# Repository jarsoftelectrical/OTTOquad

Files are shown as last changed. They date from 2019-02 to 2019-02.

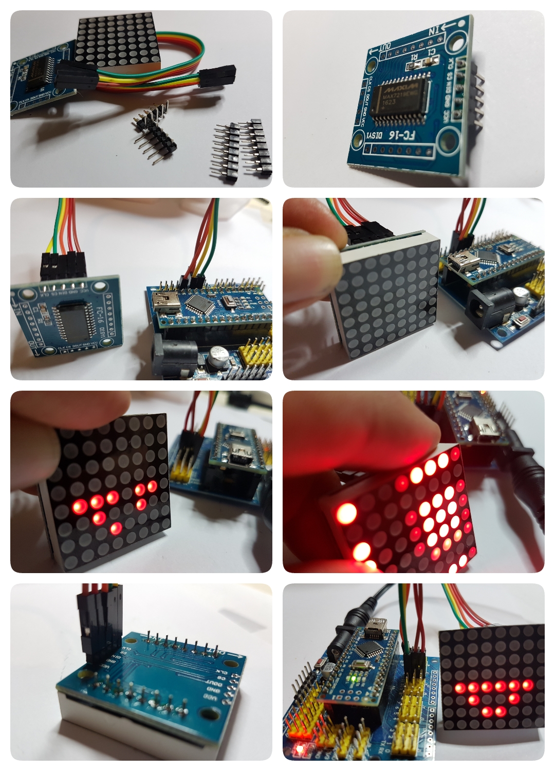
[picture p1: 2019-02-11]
Assembly/2017122816261731570.jpg

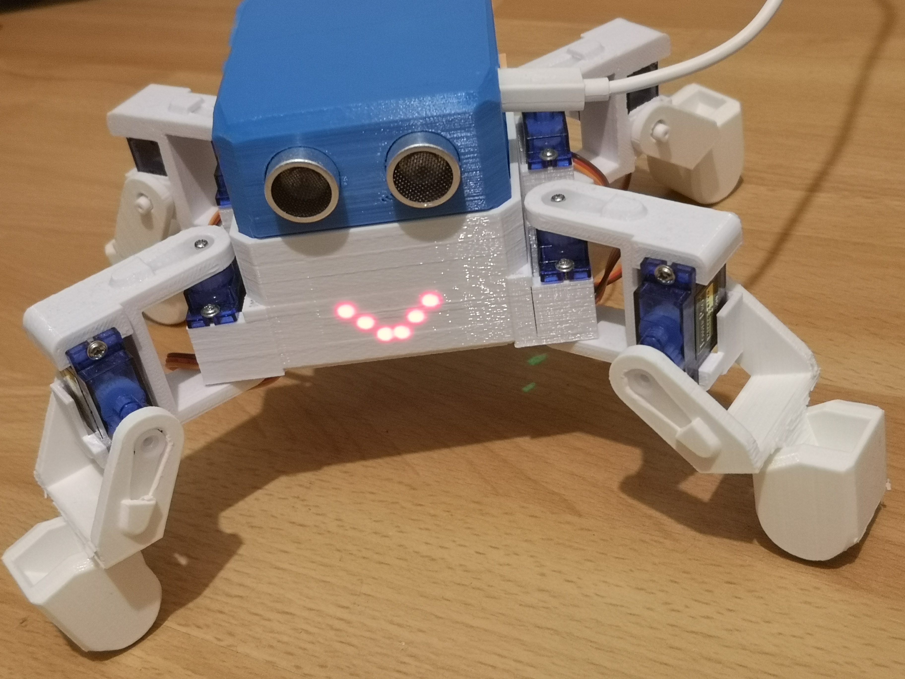
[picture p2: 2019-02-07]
Pictures/IMG_20190207_202704 1.jpg

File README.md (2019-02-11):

# OTTO Quad Code and STL files   firmware 9

Arduino Libraries and Sketch, Some basic instructions also included

## Info

Otto Quad

Compatible with parts of the OTTO android APP and the OTTO desktop control which can be downloaded from another of my repros (windows OS only)

As an open source library, Otto and Myself respect all contributors to the open source community and thank you very much for everyone's supervision.

If you have a question then please post it to the Otto Builder facebook group, this is also a great place for help and advice.

### How to print:
You will to print:
- 1 x Head (two versions available, Nano I/O shield and GSTDuino)
- 1 x Body 7 A (body)
- 2 x M-Hips (Legs)
- 2 x M-Hips SHAFTS (Pins - 4 needed in total)
- 1 x M-Body SHAFTS (Pins - 4 needed in total)
- 2 x Single_foot_typeA
- 2 x Single_foot_typeB (feet)

Print your Otto Quad, 
- 20% infil
- supports for the feet Only as they need to printed as they are provided
- I use a RAFT to help stick to the bed, this is optional
- There should be no need to rotate any parts, print as they are shown.

### Parts Needed:

Parts required for Otto Quad, 
- 8 x SG90 SERVOS
- Arduino NANO   atmega328 version
- Arduino NANO I/O shield
- HC SR04 ultrasonic module
- MAX7219 dot matrix module
- Female to female hook-up wires
- Bluetooth module (optional)
- LIPO battery 3.7volt and a suitable DC-DC converter module (optional)
- GSTDUINO PCB (instead of the Arduino Nano and shield, OPTIONAL)

### Revision of history:

Software Version 9 of the libraries, initial release

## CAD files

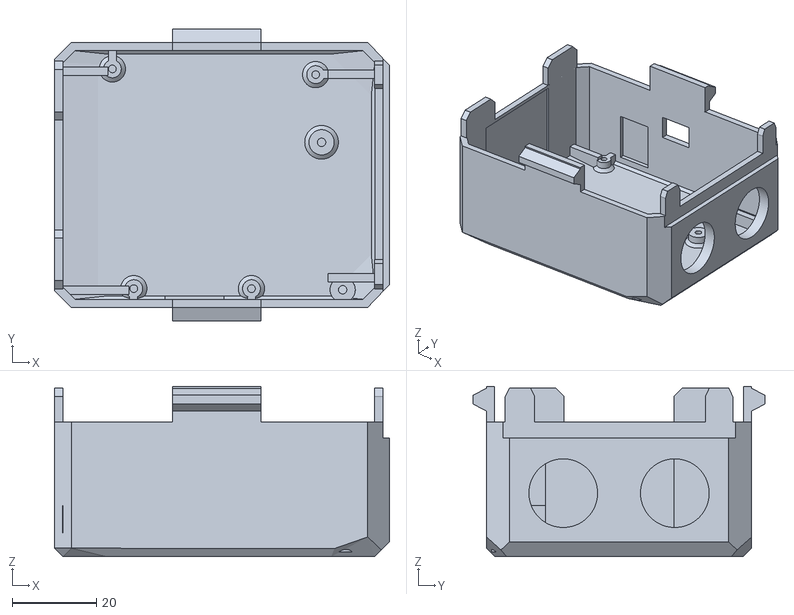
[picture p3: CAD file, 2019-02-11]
STL/Head_NANO_SHIELD.stl
79.5 x 69.2 x 40.4

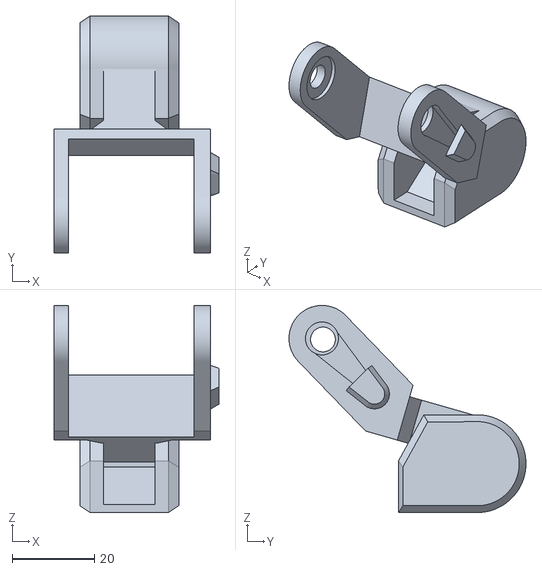
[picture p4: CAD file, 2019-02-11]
STL/Single_foot _typeA.stl
40.0 x 57.5 x 50.2

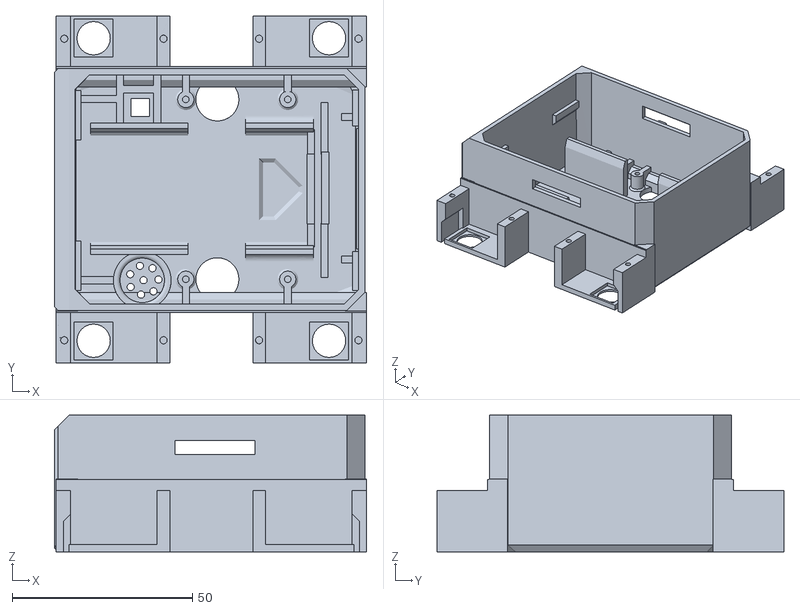
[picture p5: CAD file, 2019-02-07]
STL/Body_7A.stl
86.5 x 96.1 x 37.9

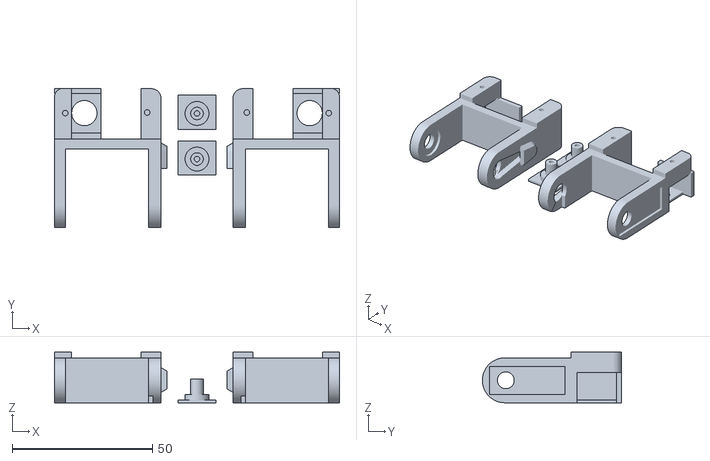
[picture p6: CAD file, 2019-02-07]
STL/m-hips.stl
101.5 x 49.6 x 18.0

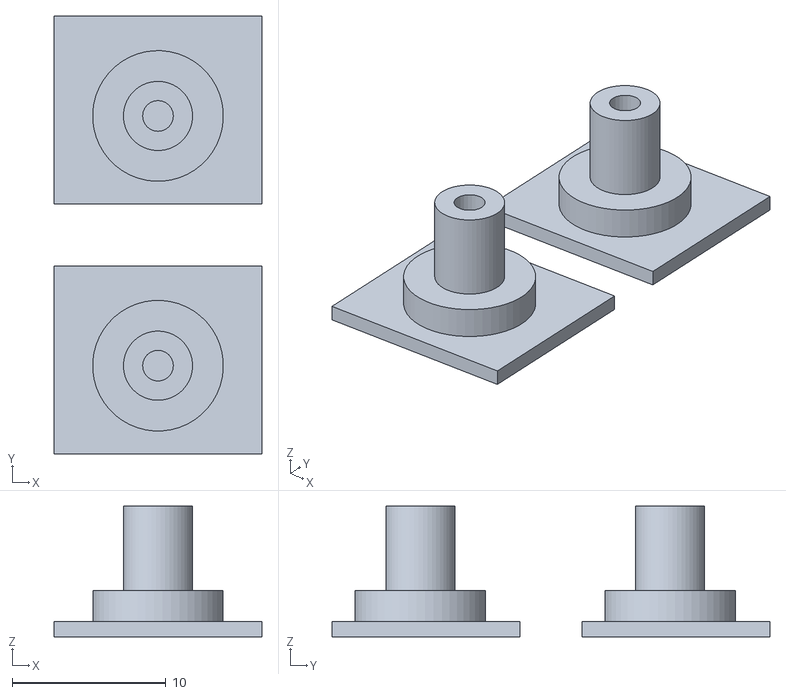
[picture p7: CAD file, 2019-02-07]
STL/m-hips_SHAFTS.stl
13.5 x 28.5 x 8.50

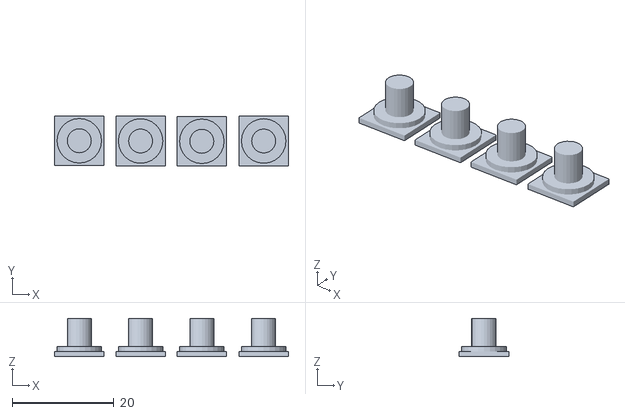
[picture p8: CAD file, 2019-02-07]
STL/m-body-shafts.stl
46.0 x 9.86 x 7.50

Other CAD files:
STL/Single_foot _typeB.stl
STL/Head.stl

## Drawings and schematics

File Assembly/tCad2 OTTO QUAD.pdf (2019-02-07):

## ULTRASONIC MODULE

## SERVO'S

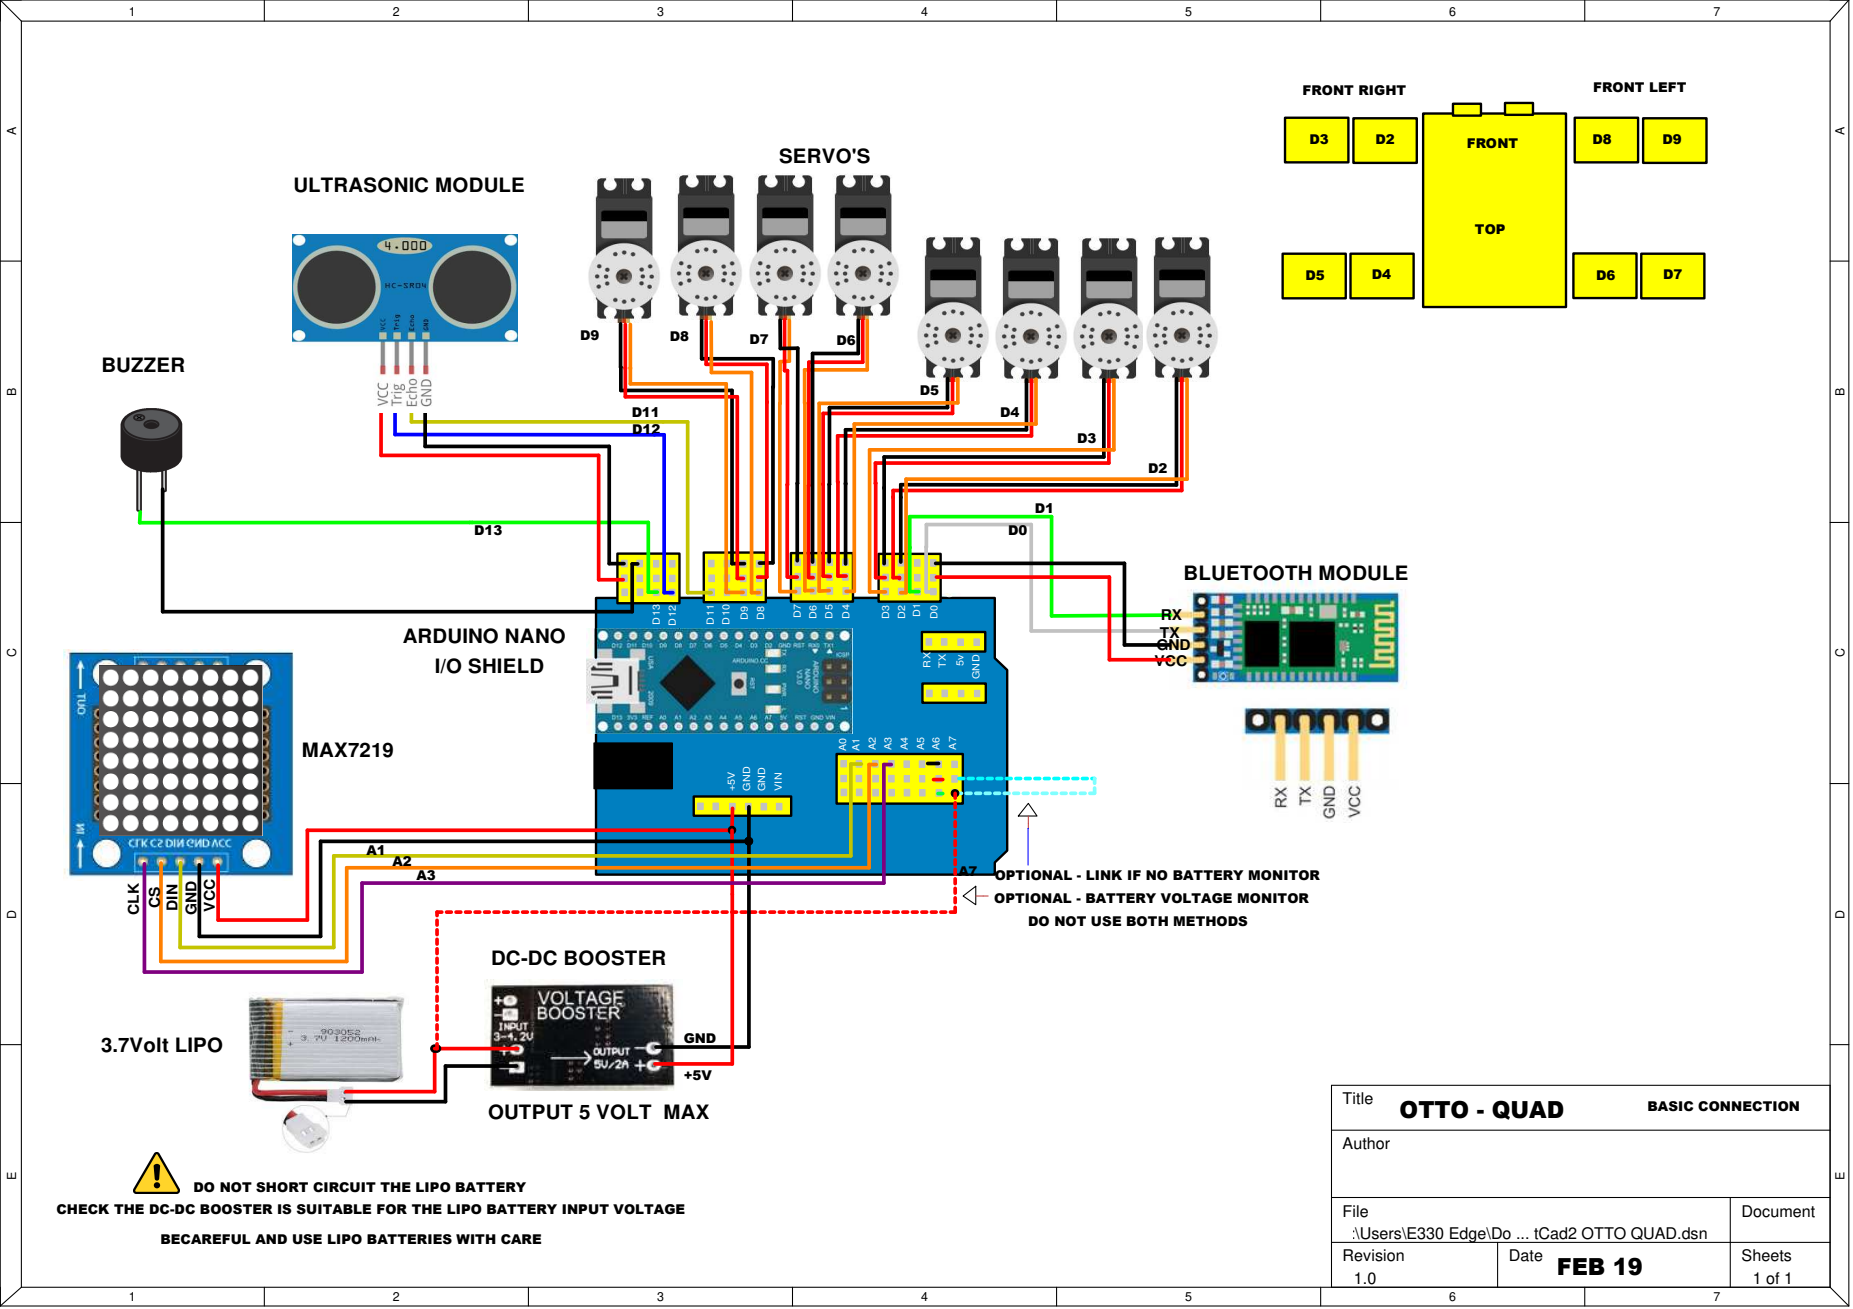
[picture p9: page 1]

A1
A2
A3

OPTIONAL - LINK IF NO BATTERY MONITOR

OPTIONAL - BATTERY VOLTAGE MONITOR

DO NOT USE BOTH METHODS

DO NOT SHORT CIRCUIT THE LIPO BATTERY

CHECK THE DC-DC BOOSTER IS SUITABLE FOR THE LIPO BATTERY INPUT VOLTAGE

File C:\Users\E330 Edge\Do ... tCad2 OTTO QUAD.dsn | Document

BECAREFUL AND USE LIPO BATTERIES WITH CARE

Revision 1.0 | Date FEB 19 | Sheets 1 of 1

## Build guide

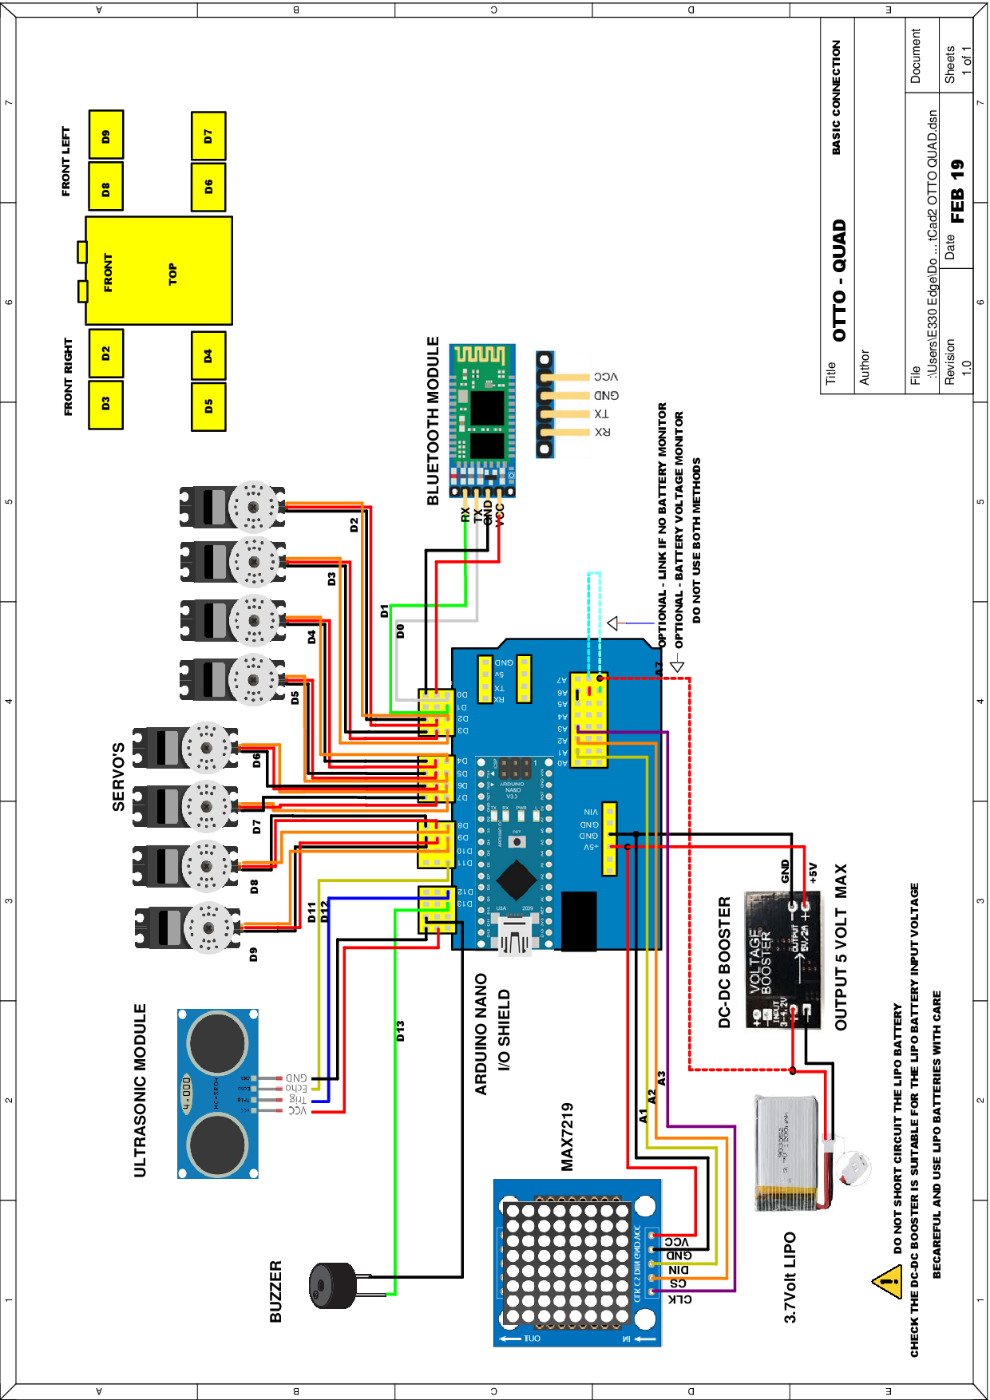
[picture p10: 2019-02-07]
Assembly/tCad2 OTTO QUAD.png

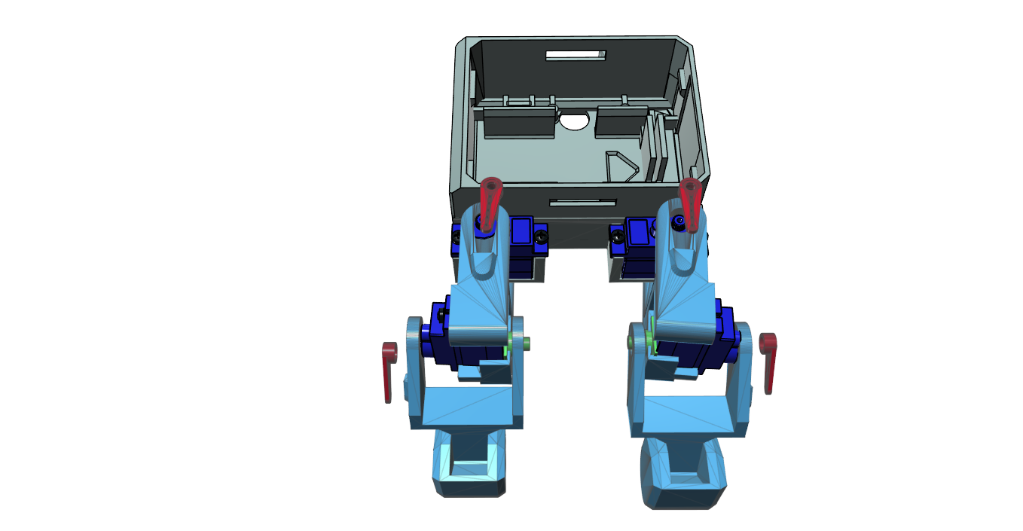
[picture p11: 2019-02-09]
Assembly/Assembly_6.png

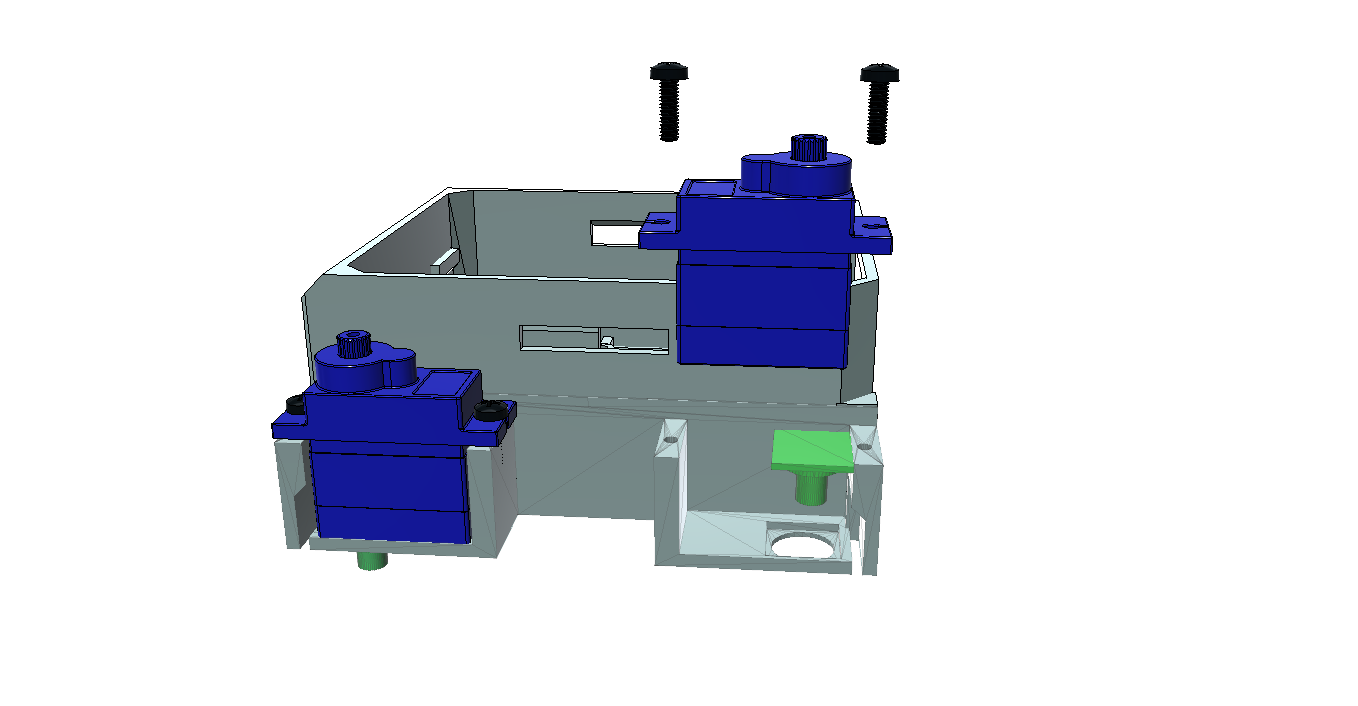
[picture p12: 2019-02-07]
Assembly/Assembly_2.png

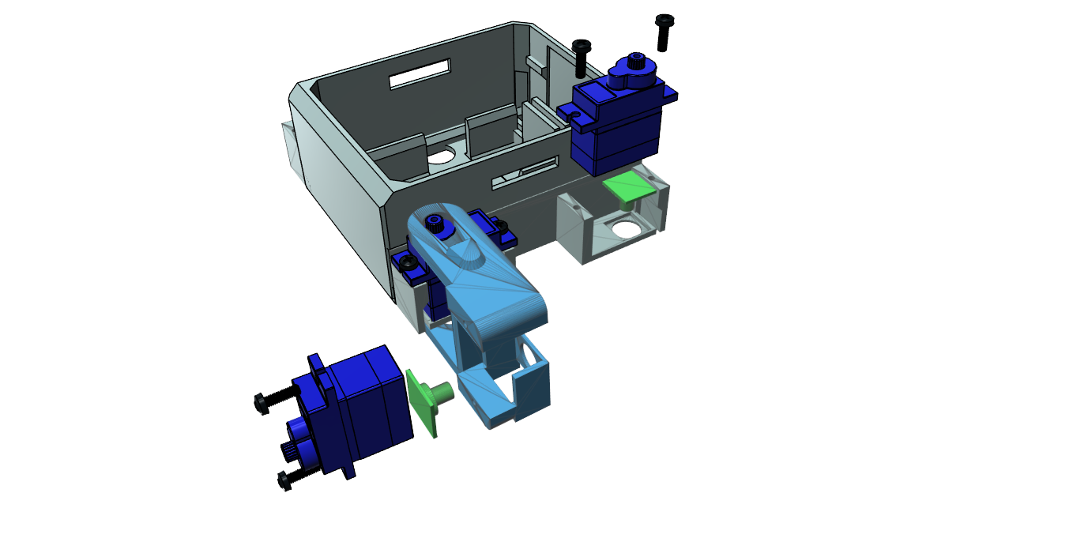
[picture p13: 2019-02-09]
Assembly/Assembly_3.png

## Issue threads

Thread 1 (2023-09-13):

Error in the model: Body_7A.stl

tekasijimo, 2023-09-13:
Hello friend! There is an error in the Body_7A.stl model! One of the sides for mounting the servo is not fully connected to the main part of the case. Because of this, when printing, it is printed as a separate element and is not connected to the case. I could fix this if there were sources, since editing the STL is inconvenient and my software does not allow doing it in an adequate way. If it is possible, in addition to the STL, add another folder with OBJ files, then it will be easier to eliminate errors and also allow you to upgrade the case for other elements.
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

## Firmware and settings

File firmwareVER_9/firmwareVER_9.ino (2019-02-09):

#include <setjmp.h>
//#include "US.h"
#include "OTTOKame.h"
#include "MaxMatrix.h"
MaxMatrix ledmatrix=MaxMatrix(A1,A2,A3, 1); //PIN  A1=DIN, PIN A2=CS, PIN A3=CLK
//-- Library to manage serial commands
#include <OttoSerialCommand.h>
OttoSerialCommand SerialCmd;  //The SerialCommand object


#define CAL_TRIGGER_PIN 10 // link this PIN 10 to +5V to enter set up mode
#define LED_PIN 13
#define PIN_Buzzer  13
//#define PIN_NoiseSensor A6
//#define battery A7
#define TIME_INTERVAL 5000
/*
   (servo PIN CONNECTIONS)
   __________ __________ _________________
  |(pin9)_____)(pin8)  (pin2)(______(pin3)|
  |__|       |left FRONT right|        |__|
             |                |
             |                |
             |                |
   _________ |                | __________
  |(pin7)_____)(pin6)__(pin4)(______(pin5)|
  |__|                                 |__|
  
ULTRASONIC PIN_Trigger 12
ULTRASONIC PIN_Echo    11
BUZZER PIN 13
*/
MiniKame robot;
bool obstacleDetected = false;
int T=1000;              //Initial duration of movement
int moveId=0;            //Number of movement
int modeId=0;            //Number of mode
int moveSize=15;         //Asociated with the height of some movements
bool auto_mode = false;
bool random_walk = false;
bool stopSerial = false;
unsigned long cur_time, prev_serial_data_time, perv_sensor_time;
char cmd = 's';
static char prev_cmd = '.';
const char programID[]="Otto_KAME7"; //Each program will have a ID
jmp_buf jump_env;
int randomDance=0;
//---------------------------------------------------------
//-- Otto has 5 modes:
//--    * MODE = 0: Otto is awaiting  
//--    * MODE = 1: Dancing mode!  
//--    * MODE = 2: Obstacle detector mode  
//--    * MODE = 3: Noise detector mode   
//--    * MODE = 4: OttoPAD or any Teleoperation mode (listening SerialPort). 
//---------------------------------------------------------
volatile int MODE=4; //State of Otto in the principal state machine. 

void setup() {
  
  //Serial communication initialization
  Serial.begin(9600);  
  // set up Matrix display
  ledmatrix.init();
  ledmatrix.setIntensity(1);

  randomSeed(analogRead(A6));
  //
  robot.init(PIN_Buzzer);
  delay(2000);
  //MY servo 2 needed to be reversed so we do it here after the init 
  //robot.reverseServo(0);
  //robot.reverseServo(1);
  robot.reverseServo(2);
  //robot.reverseServo(3);
  //robot.reverseServo(4);
  //robot.reverseServo(5);
  //robot.reverseServo(6);
  //robot.reverseServo(7);
  { //begin:  servo calibrating if PIN 10 is HIGH
    bool state = true;
    pinMode(CAL_TRIGGER_PIN, OUTPUT);
    digitalWrite(CAL_TRIGGER_PIN, 0);
    pinMode(CAL_TRIGGER_PIN, INPUT);
    while (digitalRead(CAL_TRIGGER_PIN)) {
       robot.home();//Otto HOME position
      digitalWrite(LED_PIN, 1); // on calibrating SOUND BUZZER, sounds every 2 seconds
      delay(100);
      digitalWrite(LED_PIN, 0); // off calibrating STOP BUZZER
      delay(2000);
      robot.refresh();
      state = !state;
    }
    digitalWrite(LED_PIN, 0); // off calibrating STOP BUZZER
  }//end:
  perv_sensor_time = prev_serial_data_time = millis();
  //robot.run();
  //robot.turnL();
  //robot.turnR();
  //robot.pushUp();
  //robot.upDown();
  //robot.dance();
  //robot.frontBack();
  //robot.moonwalkL();
  //robot.omniWalk();
  //robot.hello();
  //robot.jump();
  // Animation Uuuuuh - A little moment of initial surprise
 //-----
  for(int i=0; i<2; i++){
      for (int i=0;i<8;i++){  
        robot.putAnimationMouth(littleUuh,i);
        delay(150);
      }
  }
    //Smile for a happy Otto :)
    robot.putMouth(smile);
    robot.sing(S_happy);
    delay(200);  

    //Setup callbacks for SerialCommand commands 
  SerialCmd.addCommand("S", receiveStop);      //  sendAck & sendFinalAck
  SerialCmd.addCommand("L", receiveLED);       //  sendAck & sendFinalAck
  SerialCmd.addCommand("M", receiveMovement);  //  sendAck & sendFinalAck
  SerialCmd.addCommand("H", receiveGesture);   //  sendAck & sendFinalAck
  SerialCmd.addCommand("K", receiveSing);      //  sendAck & sendFinalAck
  SerialCmd.addCommand("D", requestDistance);
  //SCmd.addCommand("B", requestBattery);   // 
  SerialCmd.addCommand("I", requestProgramId);
  SerialCmd.addCommand("J", requestMode);
  SerialCmd.addDefaultHandler(receiveStop);
}
///////////////////////////////////////////////////////////////////
//-- Principal Loop ---------------------------------------------//
///////////////////////////////////////////////////////////////////
void loop() {

 if (Serial.available()>0 && MODE!=4){
    SerialCmd.readSerial();  
    //MODE=4;
    robot.putMouth(happyOpen);
  }
  
    switch (MODE) {

      //-- MODE 0 - Otto is awaiting
      //---------------------------------------------------------
      case 0:
      

        break;
      

      //-- MODE 1 - Dance Mode!
      //---------------------------------------------------------
      case 1:
        randomDance=random(5,15); //5,20
       if (randomDance == 5) randomDance = 6;
        robot.putMouth(random(10,21));
        robot.home();//Otto stop
        pause(750);
        gaits(randomDance);
        
        pause(8000);
        break;


      //-- MODE 2 - Obstacle detector mode
      //---------------------------------------------------------
      case 2:
       robot.run(0); //Otto walk straight
            //robot.refresh();
            robot.putMouth(smile);
            pause(500);
            obstacleDetector();
            pause(500);
            
        if(obstacleDetected){

             robot.home();//Otto stop
             robot.putMouth(bigSurprise);
             pause(3000);
             robot.putMouth(xMouth);
             robot.run(1); //Otto walk back
             pause(3000);
             robot.putMouth(sad);
             robot.home();//Otto stop
             pause(3000);
             robot.turnL(1, 550);
             pause(3000);
             obstacleDetector();
        }

          robot.refresh();
        break;


      //-- MODE 3 - Noise detector mode
      //---------------------------------------------------------  
      case 3:
       
        
        break;
        

      //-- MODE 4 - OttoPAD or any Teleoperation mode (listening SerialPort) 
      //---------------------------------------------------------
      case 4:

        SerialCmd.readSerial();
        
        //If Otto is moving yet
        if (robot.getRestState()==false){  
          //move(moveId);
         
          gaits(moveId);
        }

         
          
       robot.refresh();
      
        break;      


      default:
          MODE=0;
          break;
    }

}
//////////////////////////////////////////////////////////////////////////
void  gaits(int cmd) 
{
  
  bool manualMode = false;
    
    bool taken = true;
    if (prev_cmd == cmd) return;

    switch (cmd) 
    {
      case 1:
      //MiniKame::run(int dir, float steps, float T) 
        robot.run(0);
        break;
      case 2:
        robot.run(1);
        break;
      case 3:
        robot.turnL(1, 550);
        break;
      case 4:
        robot.turnR(1, 550);
        break;
      case 5:
        robot.home();
        break;
      case 6:
        robot.pushUp();
        break;
      case 7:
        robot.upDown();
        break;
      case 8:
        robot.waveHAND();
        break;
      case 9:
        robot.Hide();
        break;
      case 10:
        robot.omniWalk(true);
        break;
      case 11:
        robot.omniWalk(false);
        break;
      case 12:
        robot.dance(1, 1000);
        break;
      case 13:
       robot.frontBack(1, 750);
        break;
      case 14:
       robot.jump();
        break;
        case 15:
       robot.scared();
        break;

      default:
        taken = false;
        manualMode = true;
    }
     if(!manualMode){
    sendFinalAck();

  }
  if (taken) prev_cmd = cmd;
  return taken;
}
////////////////////////////////////////////////////////////////////
void pause(int period) 
  {
    long timeout = millis() + period;
    do 
      {
      robot.refresh();
    } 
    while (millis() <= timeout);
  }
///////////////////////////////////////////////////////////////////
//-- Functions --------------------------------------------------//
///////////////////////////////////////////////////////////////////

//-- Function to read distance sensor & to actualize obstacleDetected variable
void obstacleDetector(){

   int distance = robot.getDistance();

        if(distance<15){
          obstacleDetected = true;
        }else{
          obstacleDetected = false;
        }
}
//-- Function to receive Stop command.
void receiveStop(){

    sendAck();
    robot.home();
    prev_cmd  = '.';
    sendFinalAck();

}
//-- Function to send Ack comand (A)
void sendAck(){

  delay(30);

  Serial.print(F("&&"));
  Serial.print(F("A"));
  Serial.println(F("%%"));
  Serial.flush();
}


//-- Function to send final Ack comand (F)
void sendFinalAck(){

  delay(30);

  Serial.print(F("&&"));
  Serial.print(F("F"));
  Serial.println(F("%%"));
  Serial.flush();
}
//-- Function to receive movement commands
void receiveMovement(){
    sendAck();
    
    if (robot.getRestState()==true){
        robot.setRestState(false);
    }

    robot.clearMouth();
    //Definition of Movement Bluetooth commands
    //M  MoveID  T   MoveSize  
    char *arg; 
    arg = SerialCmd.next(); 
    if (arg != NULL) {
      moveId=atoi(arg);
      robot.putMouth(smile);
      }
    else{
      robot.putMouth(xMouth); // bad command
      delay(2000);
      robot.clearMouth();
      moveId=0; //stop
    }
    
    arg = SerialCmd.next(); 
    if (arg != NULL) {T=atoi(arg);}
    else{
      T=1000;
    }

    arg = SerialCmd.next(); 
    if (arg != NULL) {moveSize=atoi(arg);}
    else{
      moveSize =15;
    }
}
//-- Function to receive LED commands
void receiveLED(){  

    //sendAck & stop if necessary
    sendAck();
    robot.home();

    //Examples of receiveLED Bluetooth commands
    //L 000000001000010100100011000000000
    //L 001111111111111111111111111111111 (todos los LED encendidos)
    unsigned long int matrix;
    char *arg;
    char *endstr;
    arg=SerialCmd.next();
    //Serial.println (arg);
    if (arg != NULL) {
      matrix=strtoul(arg,&endstr,2);    // Converts a char string to unsigned long integer
      robot.putMouth(matrix,false);
    }else{
      robot.putMouth(xMouth); // bad command
      delay(2000);
      robot.clearMouth();
    }

    sendFinalAck();

}
//-- Function to receive sing commands
void receiveSing() {
  //sendAck & stop if necessary
  sendAck();
   robot.home();

  //Definition of Sing Bluetooth commands
  //K  SingID
  int sing = 0;
  char *arg;
  arg = SerialCmd.next();
  if (arg != NULL) sing = atoi(arg);
  else  {
  robot.putMouth(xMouth); // bad command   
  delay(2000); // 
  robot.clearMouth();
  }
  

  switch (sing) {
    case 1: //K 1
      robot.sing(S_connection);
      break;
    case 2: //K 2
      robot.sing(S_disconnection);
      break;
    case 3: //K 3
      robot.sing(S_surprise);
      break;
    case 4: //K 4
      robot.sing(S_OhOoh);
      break;
    case 5: //K 5
      robot.sing(S_OhOoh2);
      break;
    case 6: //K 6
      robot.sing(S_cuddly);
      break;
    case 7: //K 7
      robot.sing(S_sleeping);
      break;
    case 8: //K 8
      robot.sing(S_happy);
      break;
    case 9: //K 9
      robot.sing(S_superHappy);
      break;
    case 10: //K 10
      robot.sing(S_happy_short);
      break;
    case 11: //K 11
      robot.sing(S_sad);
      break;
    case 12: //K 12
      robot.sing(S_confused);
      break;
    case 13: //K 13
      robot.sing(S_fart1);
      break;
    case 14: //K 14
      robot.sing(S_fart2);
      break;
    case 15: //K 15
      robot.sing(S_fart3);
      break;
    case 16: //K 16
      robot.sing(S_mode1);
      break;
    case 17: //K 17
      robot.sing(S_mode2);
      break;
    case 18: //K 18
      robot.sing(S_mode3);
      break;
    case 19: //K 19
      robot.sing(S_buttonPushed);
      break;
    default:
      break;
  }
  sendFinalAck();
}

//-- Function to send ultrasonic sensor measure (distance in "cm")
void requestDistance(){

    robot.home();  //stop if necessary  

    int distance = robot.getDistance();
    Serial.print(F("&&"));
    Serial.print(F("D "));
    Serial.print(distance);
    Serial.println(F("%%"));
    Serial.flush();
}
//-- Function to send battery voltage percent
void requestBattery(){

    robot.home();  //stop if necessary

    //The first read of the batery is often a wrong reading, so we will discard this value. 
    double batteryLevel = robot.getBatteryLevel();

    Serial.print(F("&&"));
    Serial.print(F("B "));
    Serial.print(batteryLevel);
    Serial.println(F("%%"));
    Serial.flush();
}


//-- Function to send program ID
void requestProgramId(){

    robot.home();   //stop if necessary

    Serial.print(F("&&"));
    Serial.print(F("I "));
    Serial.print(programID);
    Serial.println(F("%%"));
    Serial.flush();
}
//-- Function to receive mode selection.
void requestMode(){

    sendAck();
    robot.home();
    //Definition of Mode Bluetooth commands
    //J ModeID    
    char *arg; 
    arg = SerialCmd.next(); 
    if (arg != NULL) 
    {
      modeId=atoi(arg);
      robot.putMouth(heart);
      delay(1000);
      robot.clearMouth();
      }
    else{
      robot.putMouth(xMouth); // bad command
      delay(2000);
      robot.clearMouth();
      modeId=0; //stop
    }
switch (modeId) {
      case 0: //
        MODE = 0;
        break;
      case 1: //
        MODE = 1;
        robot.sing(S_mode1);
        robot.putMouth(one);
        delay(1000);
    delay(200);
        break;
        case 2: //
        MODE = 2;
        robot.sing(S_mode2);
        robot.putMouth(two);
        delay(1000);
        break;
        case 3: //
        MODE = 3;
        robot.sing(S_mode3);
        robot.putMouth(three);
        delay(1000);        
        break;
        case 4: //
        robot.sing(S_mode1);
        robot.putMouth(four);
        delay(1000);       
        MODE = 4;
        break;
     default:
        MODE = 0;
        break;
   }
sendFinalAck();
robot.clearMouth();
robot.putMouth(smile);

}
 
//-- Function to receive gesture commands
void receiveGesture(){

    //sendAck & stop if necessary
    sendAck();
    robot.home(); 

    //Definition of Gesture Bluetooth commands
    //H  GestureID  
    int gesture = 0;
    char *arg; 
    arg = SerialCmd.next(); 
    if (arg != NULL) {gesture=atoi(arg);}
    else 
    {
      robot.putMouth(xMouth);
      delay(2000);
      robot.clearMouth();
    }

    switch (gesture) {
      case 1: //H 1 
        robot.playGesture(OttoHappy);
        break;
      case 2: //H 2 
        robot.playGesture(OttoSuperHappy);
        break;
      case 3: //H 3 
        robot.playGesture(OttoSad);
        break;
      
      case 7: //H 7 
        robot.playGesture(OttoLove);
        break;   
      
        
      default:
        break;
    }

    sendFinalAck();
}

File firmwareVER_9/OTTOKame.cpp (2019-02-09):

#include <EEPROM.h>
#include "OTTOKame.h"

/*
   (servo index, pin to attach pwm)
   __________ __________ _________________
  |(3,9)_____)(1,8)      (0,2)(______(2,3)|
  |__|       |left FRONT right|        |__|
             |                |
             |                |
             |                |
   _________ |                | __________
  |(7,7)_____)(5,6)______(4,4)(______(6,5)|
  |__|                                 |__|

*/
//comment below manually setting trim in MiniKame() constructor
#define __LOAD_TRIM_FROM_EEPROM__
#define EEPROM_MAGIC  0xabcd
#define EEPROM_OFFSET 2   //eeprom starting offset to store trim[]

// FRONT_RIGHT_HIP servo 0  Pin 2
// FRONT_LEFT_HIP servo 1  Pin 8
// FRONT_RIGHT_LEG servo 2  Pin 3
// FRONT_LEFT_LEG servo 3  Pin 9
// BACK_RIGHT_HIP servo 4  Pin 4
// BACK_LEFT_HIP servo 5  Pin 6
// BACK_RIGHT_LEG servo 6  Pin 5
// BACK_LEFT_LEG servo 7  Pin 7
MiniKame::MiniKame():/* reverse{0, 0, 0, 0, 0, 0, 0, 0}, */trim{0, 0, 0, 0, 0, 0, 0, 0} {
  board_pins[FRONT_RIGHT_HIP] = 2; // front left inner
  board_pins[FRONT_LEFT_HIP] = 8; // front right inner
  board_pins[BACK_RIGHT_HIP] = 4; // back left inner
  board_pins[BACK_LEFT_HIP] = 6; // back right inner
  board_pins[FRONT_RIGHT_LEG] = 3; // front left outer
  board_pins[FRONT_LEFT_LEG] = 9; // front right outer
  board_pins[BACK_RIGHT_LEG] = 5; // back left outer
  board_pins[BACK_LEFT_LEG] = 7; // back right outer
}
void MiniKame::reverseServo(int id) {
  if (reverse[id])
    reverse[id] = 0;
  else
    reverse[id] = 1;
}
void MiniKame::init(int Buzzer) {
  //Buzzer & noise sensor pins: 


   //Buzzer & noise sensor pins: 
  pinBuzzer = Buzzer;
  //pinMode(NoiseSensor,INPUT);

  /*
     trim[] for calibrating servo deviation,
     initial posture (home) should like below
     in symmetric
        \       / front left
         \_____/
         |     |->
         |_____|->
         /     \
        /       \ front right
  */
  /*
    trim[FRONT_LEFT_HIP] = 0;
    trim[FRONT_RIGHT_HIP] = -8;
    trim[BACK_LEFT_HIP] = 8;
    trim[BACK_RIGHT_HIP] = 5;

    trim[FRONT_LEFT_LEG] = 2;
    trim[FRONT_RIGHT_LEG] = -6;
    trim[BACK_LEFT_LEG] = 6;
    trim[BACK_RIGHT_LEG] = 5;
  */
#ifdef __LOAD_TRIM_FROM_EEPROM__
  int val = EEPROMReadWord(0);
  if (val != EEPROM_MAGIC) {
    EEPROMWriteWord(0, EEPROM_MAGIC);
    storeTrim();
  }
#endif

  for (int i = 0; i < 8; i++) {
    servo[i].attach(board_pins[i]);

#ifdef __LOAD_TRIM_FROM_EEPROM__
    int val = EEPROMReadWord(i * 2 + EEPROM_OFFSET);
    if (val >= -90 && val <= 90) {
      trim[i] = val;
    }
#endif
  }

  home();
  us.init(12, 11);
}
void MiniKame::attachServo(){
   for (int i = 0; i < 8; i++) {
    servo[i].attach(board_pins[i]);
  }
}
void MiniKame::detachServo(){
   for (int i = 0; i < 8; i++) {
    servo[i].detach();
  }
}
void MiniKame::turnL(float steps, float T) {
  if(getRestState()==true){
        setRestState(false);
  }

  int x_amp = 15;
  int z_amp = 15;
  int ap = 15;
  //int hi = 23;
  int hi = 0;
  float period[] = {T, T, T, T, T, T, T, T};
  int amplitude[] = {x_amp, x_amp, z_amp, z_amp, x_amp, x_amp, z_amp, z_amp};
  int offset[] = {90 + ap, 90 - ap, 90 - hi, 90 + hi, 90 - ap, 90 + ap, 90 + hi, 90 - hi};
  int phase[] = {0, 180, 90, 90, 180, 0, 90, 90};

  execute(steps, period, amplitude, offset, phase);
}

void MiniKame::turnR(float steps, float T) {
  if(getRestState()==true){
        setRestState(false);
  }

  int x_amp = 15;
  int z_amp = 15;
  int ap = 15;
  int hi = 0;
  float period[] = {T, T, T, T, T, T, T, T};
  int amplitude[] = {x_amp, x_amp, z_amp, z_amp, x_amp, x_amp, z_amp, z_amp};
  int offset[] = {90 + ap, 90 - ap, 90 - hi, 90 + hi, 90 - ap, 90 + ap, 90 + hi, 90 - hi};
  int phase[] = {180, 0, 90, 90, 0, 180, 90, 90};

  execute(steps, period, amplitude, offset, phase);
}

void MiniKame::dance(float steps, float T) {
  if(getRestState()==true){
        setRestState(false);
  }
  digitalWrite(13, 0);
  int x_amp = 0;
  int z_amp = 40;
  int ap = 30;
  int hi = 0;
  float period[] = {T, T, T, T, T, T, T, T};
  int amplitude[] = {x_amp, x_amp, z_amp, z_amp, x_amp, x_amp, z_amp, z_amp};
  int offset[] = {90 + ap, 90 - ap, 90 - hi, 90 + hi, 90 - ap, 90 + ap, 90 + hi, 90 - hi};
  int phase[] = {0, 0, 0, 270, 0, 0, 90, 180};

  execute(steps, period, amplitude, offset, phase);
}

void MiniKame::frontBack(float steps, float T) {
  if(getRestState()==true){
        setRestState(false);
  }

  int x_amp = 30;
  int z_amp = 25;
  int ap = 20;
  int hi = 0;
  float period[] = {T, T, T, T, T, T, T, T};
  int amplitude[] = {x_amp, x_amp, z_amp, z_amp, x_amp, x_amp, z_amp, z_amp};
  int offset[] = {90 + ap, 90 - ap, 90 - hi, 90 + hi, 90 - ap, 90 + ap, 90 + hi, 90 - hi};
  int phase[] = {0, 180, 270, 90, 0, 180, 90, 270};

  execute(steps, period, amplitude, offset, phase);
}

void MiniKame::run(int dir, float steps, float T) {
 
        setRestState(true);

digitalWrite(13, 0);
  int x_amp = 15;
  int z_amp = 15;
  int ap = 15;
  int hi = 0;
  int front_x = 0;
  float period[] = {T, T, T, T, T, T, T, T};
  int amplitude[] = {x_amp, x_amp, z_amp, z_amp, x_amp, x_amp, z_amp, z_amp};
  int offset[] = {    90 + ap - front_x,
                      90 - ap + front_x,
                      90 - hi,
                      90 + hi,
                      90 - ap - front_x,
                      90 + ap + front_x,
                      90 + hi,
                      90 - hi
                 };
  int phase[] = {0, 0, 90, 90, 180, 180, 90, 90};
  if (dir == 1) {
    phase[0] = phase[1] = 180;
    phase[4] = phase[5] = 0;
  }
  execute(steps, period, amplitude, offset, phase);
  setRestState(false);
}

void MiniKame::omniWalk(bool side, float T, float turn_factor) {
  if(getRestState()==true){
        setRestState(false);
  }
  digitalWrite(13, 0);
  int x_amp = 15;
  int z_amp = 15;
  int ap = 15;
  int hi = 23;
  int front_x = 6 * (1 - pow(turn_factor, 2));
  float period[] = {T, T, T, T, T, T, T, T};
  int amplitude[] = {x_amp, x_amp, z_amp, z_amp, x_amp, x_amp, z_amp, z_amp};
  int offset[] = {    90 + ap - front_x,
                      90 - ap + front_x,
                      90 - hi,
                      90 + hi,
                      90 - ap - front_x,
                      90 + ap + front_x,
                      90 + hi,
                      90 - hi
                 };

  int phase[8];
  if (side) {
    int phase1[] =  {0,   0,   90,  90,  180, 180, 90,  90};
    int phase2R[] = {0,   180, 90,  90,  180, 0,   90,  90};
    for (int i = 0; i < 8; i++)
      phase[i] = phase1[i] * (1 - turn_factor) + phase2R[i] * turn_factor;
  }
  else {
    int phase1[] =  {0,   0,   90,  90,  180, 180, 90,  90};
    int phase2L[] = {180, 0,   90,  90,  0,   180, 90,  90};
    for (int i = 0; i < 8; i++)
      phase[i] = phase1[i] * (1 - turn_factor) + phase2L[i] * turn_factor;// + oscillator[i].getPhaseProgress();
  }

  execute(1, period, amplitude, offset, phase);
}
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

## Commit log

2019-02-11 Feet separated due to issues raised
    [Single_foot _typeA.stl, Single_foot _typeB.stl]
2019-02-11 Matrix assembly instructions
2019-02-11 Nano I/O shield version
    [Head_NANO_SHIELD.stl]
